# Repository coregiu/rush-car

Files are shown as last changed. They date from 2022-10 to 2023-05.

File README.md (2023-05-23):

# RUCAR
RUCAR: Rush Car

RUCAR是利用51单片机、L298N电机驱动、PS2手柄、音乐芯片、舵机云台、PWM控制模块、DIY灯组和小车底盘DIY实现的PS2摇控小车，并且可以用PS2控制的音乐播放和灯组。

## 功能说明
#### 遥控小车行驶
可通过PS2控制小车前进、后退、左转、右转。

#### 遥控音乐播放及切换
可通过PS2控制轩载音乐播放，音乐更换。

#### 遥控LED灯光效果切换
可通过PS2控制小车顶LED灯光开关和切换。
灯光效果可以有常亮、间隔闪烁等效果。

#### 遥控舵机云台变换灯光角度
将LED灯组放置云台，可以通过云台控制灯光方向。

## 设计说明

#### 硬件设计

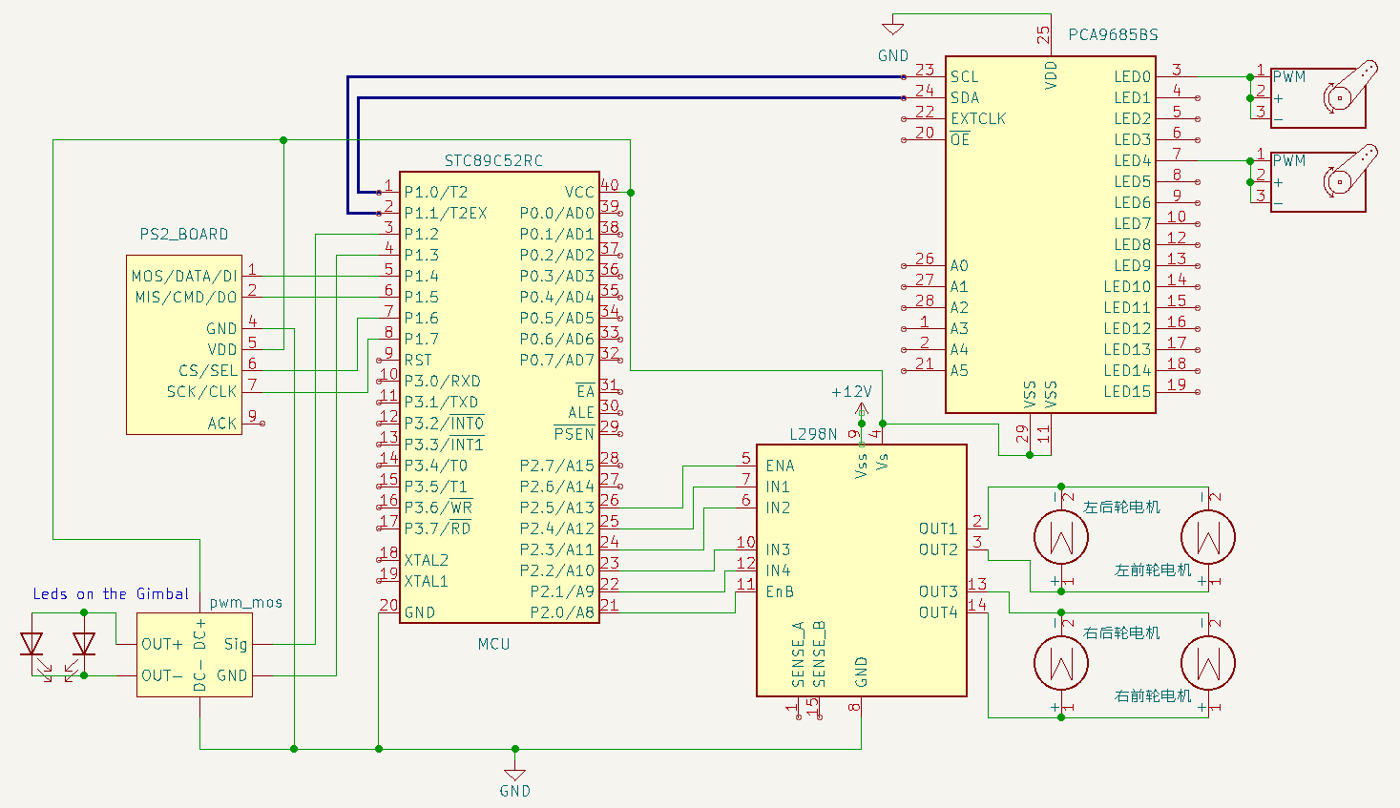
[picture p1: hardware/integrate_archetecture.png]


详细参照：[硬件设计说明](hardware/README.md)

#### 软件设计

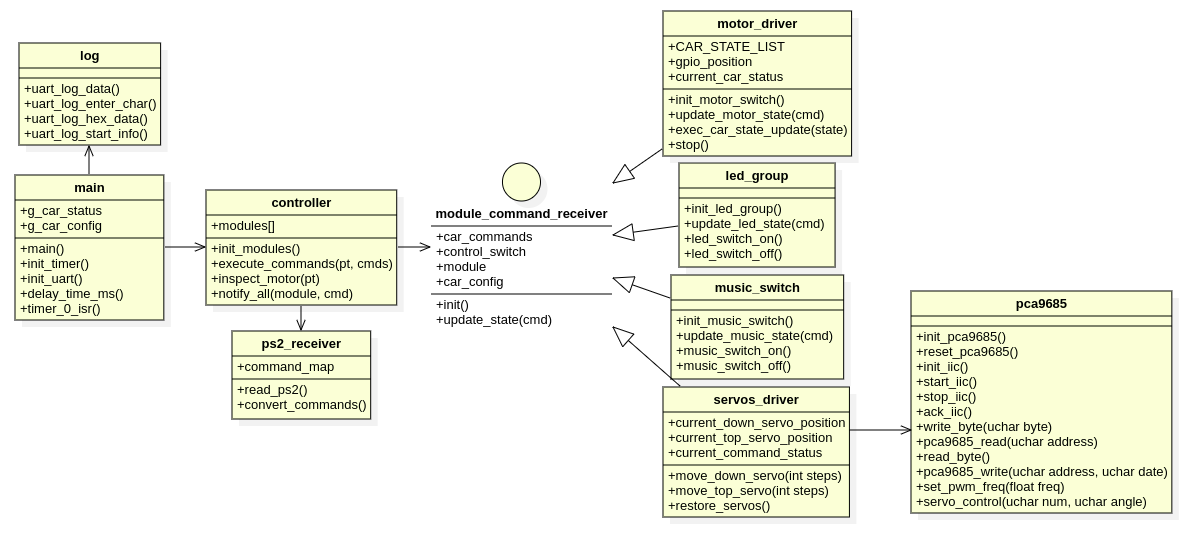
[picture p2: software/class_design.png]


详细参照：[软件设计说明和代码](software/README.md)

## PS2按键功能

| 按键 | 功能 | 监控指示灯 |
| --- | --- | --- |
| 左侧上键 | 小车前进，长按有效，放开停止 | P0_0 |
| 左侧下键 | 小车后退，长按有效，放开停止 | P0_1 |
| 左侧左键 | 小车左转，长按有效，放开停止 | P0_2 |
| 左侧右键 | 小车右转，长按有效，放开停止 | P0_3 |
| 右侧上健 | 云台前倾 | P0_4 |
| 右侧下键 | 云台后仰 | P0_5 |
| 右侧左键 | 云台左转 | P0_6 |
| 右侧右键 | 云台右转 | P0_7 |
| 左侧1键  | 云台复位 | P0_0 |
| 左侧2键  | 系统复位 | P0_1 |
| 右侧1键  | 开灯 | P0_2 |
| 右侧2键  | 关灯 | P0_3 |

## 成品效果

##### 视频

https://b23.tv/4TEsZSw

##### 正视

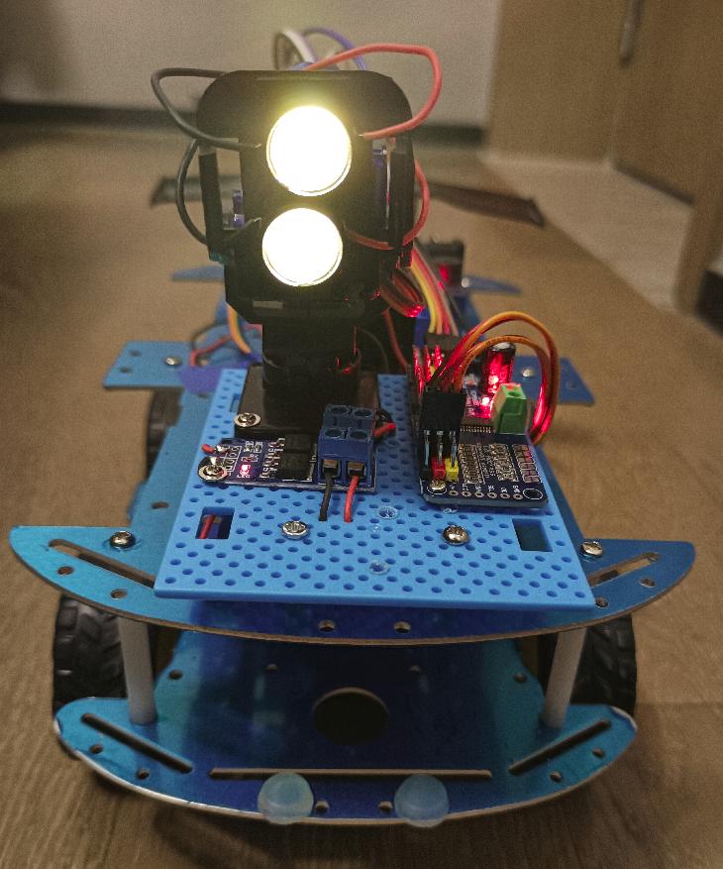
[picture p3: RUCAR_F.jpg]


##### 俯视

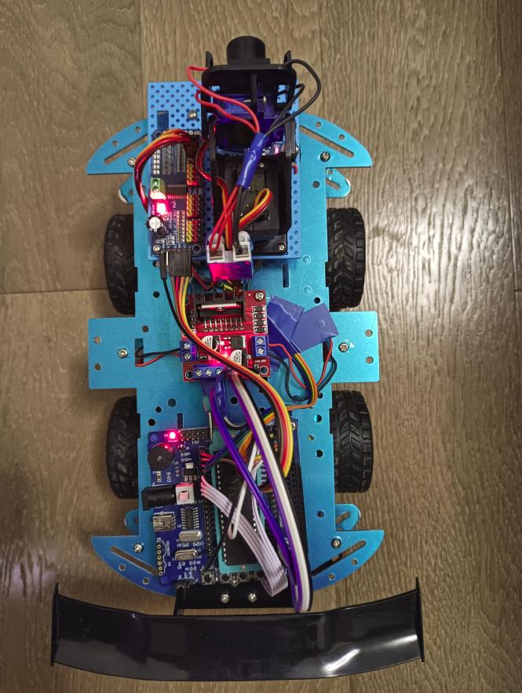
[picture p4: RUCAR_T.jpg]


##### 左视

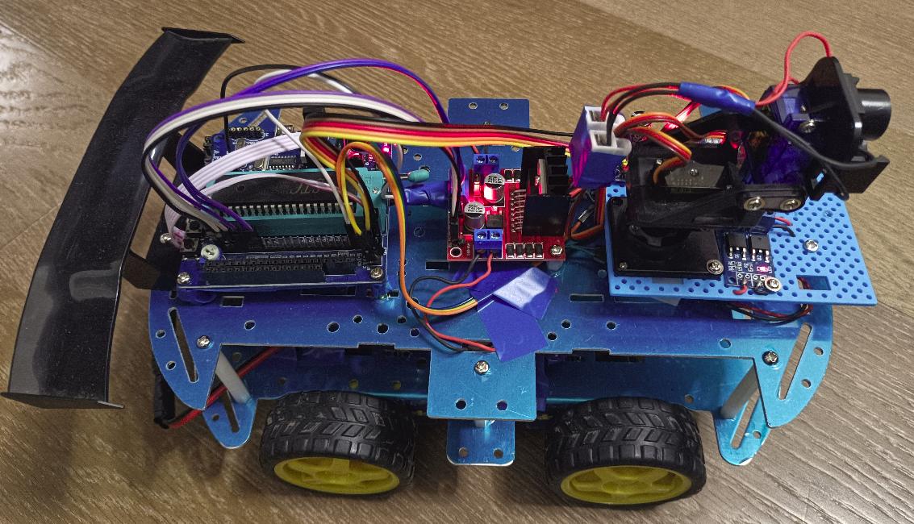
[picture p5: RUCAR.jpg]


## 硬件模块及工具清单：

| 模块 | 说明 | 价格(元) |
| --- | --- | --- |
| 51单片机 | 单片机 STC89C52RC芯片，11.0592晶振。 | 40 |
| 小车底盘 | 小车底盘及M3铜柱螺丝若干，底盘带4个直流电机。 | 30 |
| ps2手柄 | 无线的那种，会带接收器。 | 40 |
| L298N电机驱动 | 12V供电，同时带5V输出电压。 | 4 |
| 音乐芯片 | 建议用ISD1820录音的，能录20秒。需要手动焊接喇叭 | 10 |
| 音频放大器 | AD828，可以买电压针脚都焊上的，省得自己焊了。 | 10 |
| PWM信号控制器 | 信号控制开关，一定要按他说明接线 | 2 |
| DIY灯组 | DIY灯组电路包括LED灯珠/电容/电阻/三极管/PCB板等。简单搞就是正常的并联电路，复杂一点闪烁灯用电容加三极管，再复杂的流水灯用NE555和CD4017搞，这个看个人喜好。灯珠可以买七彩的，自己会自动闪烁的，效果不错。或者可以买现成的模块，或者没焊的模块回来自己焊一下。 | 10 |
| 电池及充电器  | 12V锂电池和12V充电器 | 35 |
| 各种接线 | 各种公对公，母对母杜邦线若干，DIY铜线，漆包线，转接头，接线器等 | 10 |
| sg90舵机 | 两个180度的 | 10 |
| 尼龙云台 | 注意跟舵机尺寸匹配，也可以跟舵机买全套的 | 5 |
| pca9685舵机驱动模块 | 16路驱动，好像有点浪费，但没有更小的了 | 15 |

另外音乐芯片组装需要电烙铁焊接，组装时可能需要万用表做些测试。如果对焊接不熟悉，还是买现成的模块比较合适。以上东西都可以在网上买到。

## 使用的相关工具软件：

#### OS： Ubuntu 20.04

#### 硬件设计工具KiCAD

安装：https://docs.kicad.org/5.1/zh/getting_started_in_kicad/getting_started_in_kicad.html

#### 软件设计开发工具:

- 软件设计工具： StarUML  https://staruml.io/download

- 开发IDE： VSCODE

- 编译软件： sdcc/packihx, cmake

ubuntu下安装： sudo apt-get install sdcc

- 烧录软件：stcflash

ubuntu下安装： 从社区下载到本地，社区地址：https://github.com/laborer/stcflash

将stcflash.py文件解压到/usr/local/bin。 并去掉后缀名。

- 依赖： python3, python-pip3, python serial

安装python serial: https://www.geeksforgeeks.org/how-to-install-python-serial-package-on-linux/

如果执行: stcflash报错： usr/bin/env: ‘python’: No such file or directory

执行以下命令解决： sudo ln -s /usr/bin/python3 /usr/bin/python

- 串口调试工具： comtool

安装： sudo pipe3 install comtool

# > 看到这里，说明你心动了，攒一个吧，不贵，硬件成本才200元左右。

# > 拼多多是个好东西，你想要的小器件都有，而且便宜还包邮。

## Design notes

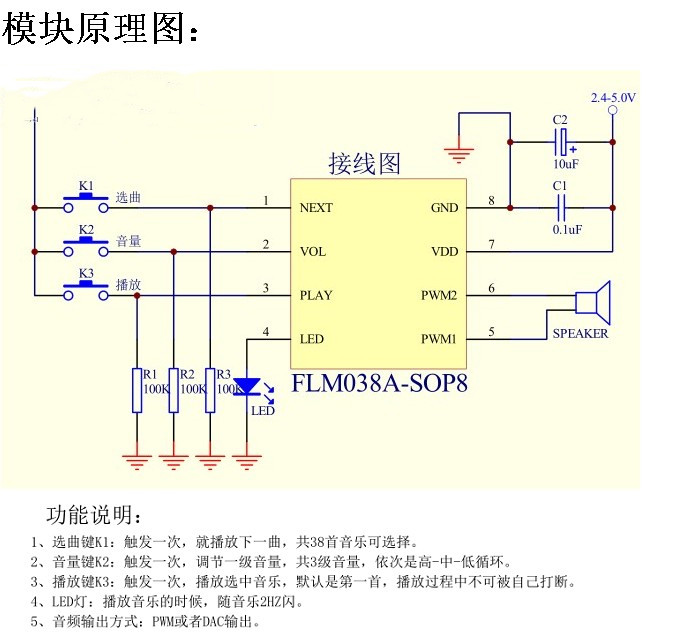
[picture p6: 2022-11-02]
hardware/modules/flm038-sop8-board.jpg

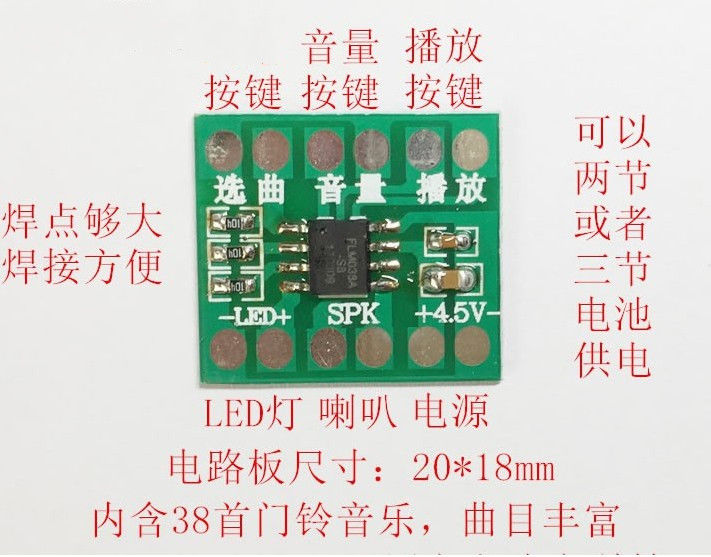
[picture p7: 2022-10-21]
hardware/modules/flm038-sop8-body.jpg

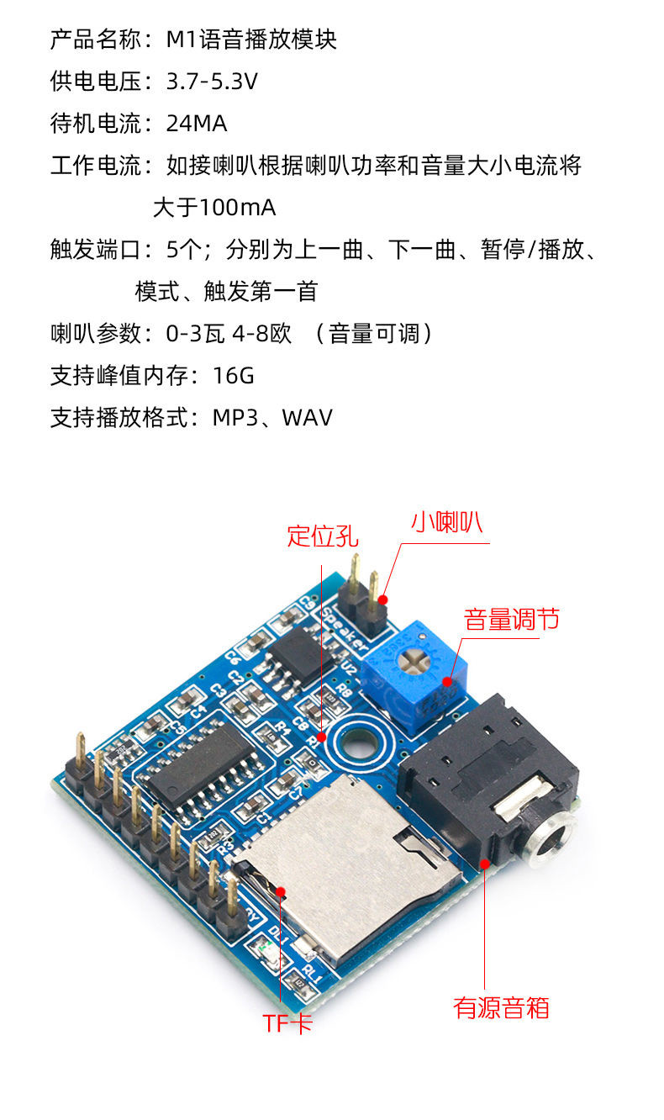
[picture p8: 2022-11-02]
hardware/modules/mp3.jpg

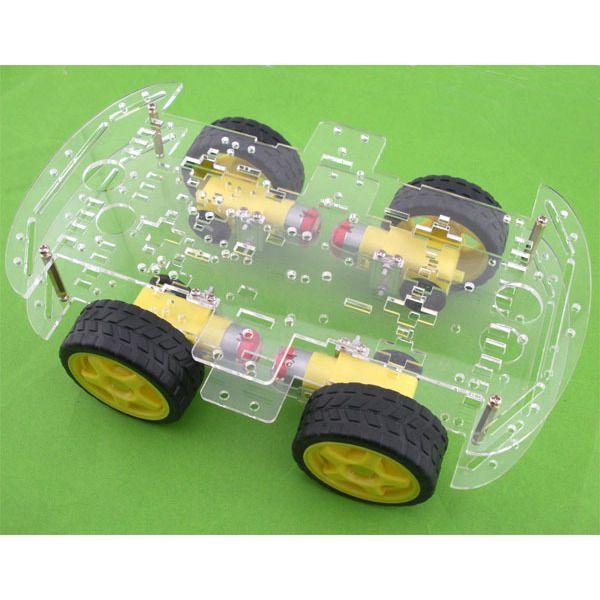
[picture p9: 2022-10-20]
hardware/modules/car.jpg

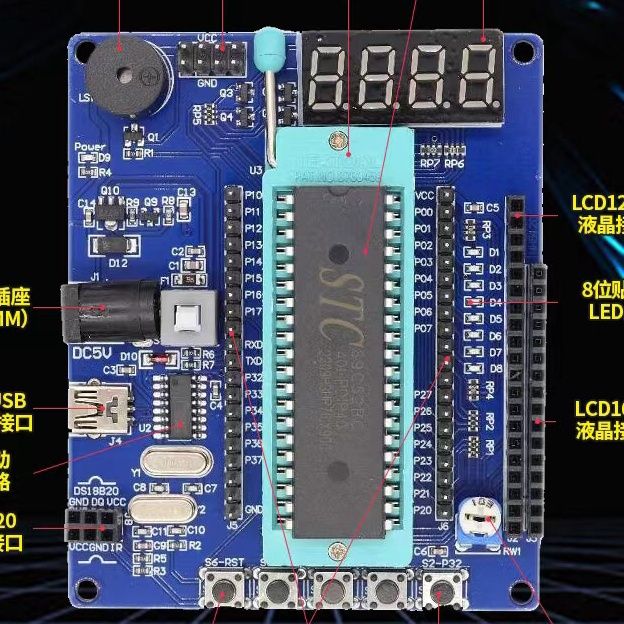
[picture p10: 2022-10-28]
hardware/modules/51mcu.jpg

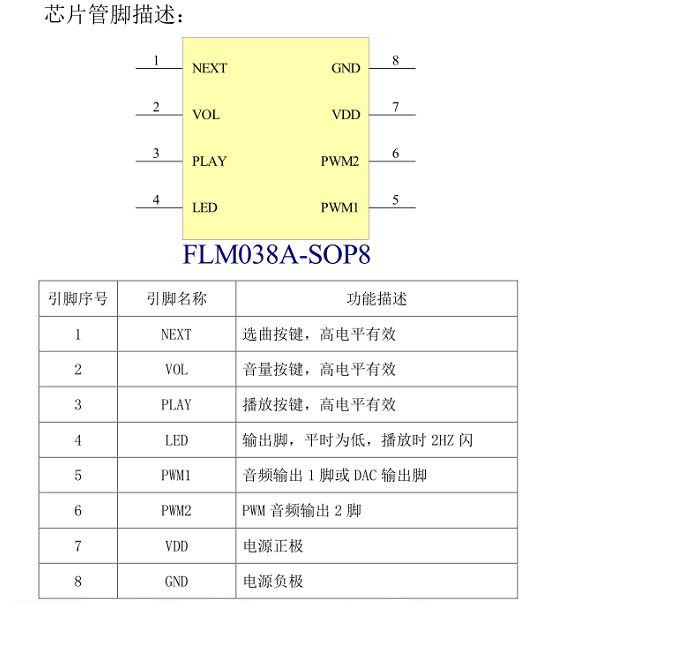
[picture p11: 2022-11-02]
hardware/modules/flm038-sop8-description.jpg

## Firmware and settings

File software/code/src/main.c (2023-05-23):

/**
  ******************************************************************************
  *
  * main function
  * author: coregiu
  * 
  * 
  ******************************************************************************
**/

#include <controller.h>
/* 71ms per period */
#define READ_PS2_INTVAL_TIME_MS_H   0X00
#define READ_PS2_INTVAL_TIME_MS_L   0X00

const struct car_config g_car_config = {READ_PS2_INTVAL_TIME_MS_H, READ_PS2_INTVAL_TIME_MS_L};

const uchar EXE_PERIODS = 1;

// delay times for timer 0. 3 times for a execute period, equals 200ms.
uchar delayTimes = 0;

void delay_time_ms(uint mil_sec)
{
	uint i, j;
	for (i = mil_sec; i > 0; i--)
		for (j = 70; j > 0; j--)
			;
}

/**
 * init timer 0.
 */
void init_timer()
{
	// init timer0
	TMOD |= 0X01;
	ET0 = 1;
    TR0 = 1;
    TH0 = g_car_config.interval_of_read_ps2_h;
    TL0 = g_car_config.interval_of_read_ps2_l; 
	EA  = 1; //开启总中断
}

/**
 * init uart.
 */
void init_uart()
{
	// init uart
	TMOD |= 0x20; //用定时器设置串口波特率	   9600
	TH1  = 0xfd;
	TL1  = 0xfd;
	TR1  = 1;
	ES   = 0;
	SCON = 0X50; 
	EA   = 1; //开启总中断
}

void main()
{
	delay_time_ms(500);

	init_timer();
	init_uart();
	init_modules();

	uart_log_start_info();

	while (1)
	{

	}
}

/**
 * timer 0 interrupt function.
 * read ps2 command and execute it by 50ms interval.
 */
void time_0_isr(void) __interrupt 1
{
	if (delayTimes < EXE_PERIODS)
	{
		delayTimes++;
		return;
	}

	// reset number of beginning.
	TH0 = g_car_config.interval_of_read_ps2_h;
	TL0 = g_car_config.interval_of_read_ps2_l;
	
	// read ps2 command and set is_has_command/non_motor_cmd_times value.
	uint commands[COMMANDS_LENGTH][2] = {{0}};
	uint is_has_command = 0;
	read_ps2(&is_has_command, commands);
	// executet the commands.
	execute_commands(is_has_command, commands); 
	delayTimes = 0;
}

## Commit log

2022-10-18 init project for racar.
    [rucar.kicad_pcb, rucar.kicad_sch]
2022-10-18 finish hardware design.
    [rucar.kicad_pcb, rucar.kicad_sch]
2022-10-19 change ps2 gnio to P1
    [rucar.kicad_sch]
2022-10-20 add description of hardware design.
    [rucar.kicad_pcb, rucar.kicad_sch]
2022-10-20 change switch to pwm module.
    [rucar.kicad_sch]
2022-10-21 change music board to flm038-sop8-body
    [rucar.kicad_sch]
2022-10-22 finish led group
2022-10-22 change led to control module.
    [rucar.kicad_sch]
2022-10-22 fix led group with monitor led.
2022-10-22 finish motor module
2022-10-22 fix some description.
    [rucar.kicad_sch]
2022-10-24 add new led circuit
2022-10-25 fix the pwm use method
    [rucar.kicad_sch]
2022-10-25 change music and led command
2022-10-25 change motor stop by 2 second
2022-10-25 fix log print.
2022-10-26 change gpio of motor driver.
    [rucar.kicad_sch]
2022-10-28 change music board to isd1820
    [rucar.kicad_sch]
2022-10-28 add filter for redundant commands.
2022-11-02 add AD828
    [rucar.kicad_sch]
2022-11-11 fix run with timer0.
2022-11-11 fix command execute with module, and using delay motor by timer1.
2022-11-11 using protothread instead of timer1.
2022-11-11 fix log print interrupt of serial port.
    [main.c]
2022-11-28 fix delay times, public 2.0
    [main.c]
2023-03-01 fix design
    [rucar.kicad_sch]
2023-05-22 v3-change to gimbal
    [rucar.kicad_sch]
2023-05-23 refactor of moving car status to motor module
